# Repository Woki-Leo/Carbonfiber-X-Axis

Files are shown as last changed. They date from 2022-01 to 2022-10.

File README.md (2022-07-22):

# Lightweight X Axis Mod for the Voron 2.4 and Trident

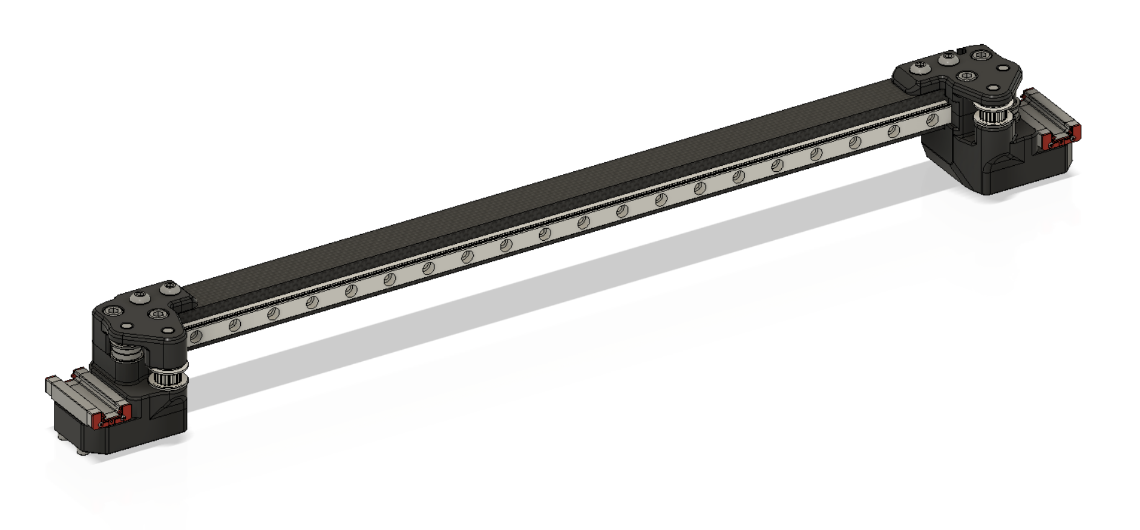
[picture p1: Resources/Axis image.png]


## What the goal is:

**Caution: the carbon tube will start soften at and above 60c chamber temperature!!**

- Removing lots of unnecessary weight to make the Printer go faster with better Quality
  - for a V2.4 350mm it drops the gantry weight from ~1350g to ~950g
    - 70g saved by removing the x drag chain
    - 150g saved by using the carbon tube
    - the rest is saved through the pinmod and other improvements
- Look good
- be usable for both MGN9 and MGN12

<br/>

## What's different:

- XY joints changes:
  - derived from the [pinmod](https://github.com/VoronDesign/VoronUsers/tree/master/printer_mods/hartk1213/Voron2.4_Pins_Mod)
  - room for MGN12 (heavily inspired by [arkeet](https://github.com/VoronDesign/VoronUsers/tree/master/printer_mods/arkeet/mgn12))
  - adjustment slots for the tube
  - removed unnecessary cutouts unter the y carriages (actually saves weight)
    - cut the corners at 45° here as well. Removes material that does nothing. 
- Chain delete --> umbilical receivers required

<br/>

## Required hardware:

- 20x20 1mm wall thickness carbon fiber tube 
  - you can use the original Alu tube as well but it will be very heavy
  - [you can find a fabricated tube here](https://www.aliexpress.com/item/1005004037790448.html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)
- 4PCs 5x40mm Pins (Use Carbon fiber rod)
- 4PCs M5x40 SHCS
- 10PCs M5 Nut
- 4PCs M5x12 BHCS
- 2PCs M5x30 BHCS

Using aluminium hardware for M5 is recommended. Watch out for the right alloy and heat treat! 7075 T6 is strongly recommended!

For rail mounting:
M3x8 SHCS + Nuts for the amount of screws you want (4-8 Recommended)

<br/>

## Required mods:

- MGN12: arkeet's [MGN12](https://github.com/VoronDesign/VoronUsers/tree/master/printer_mods/arkeet/mgn12) carriage or  jlas1' mgn12 [klicky](https://github.com/jlas1/Klicky-Probe/tree/main/Usermods/bluedragonx) carriage 
- MGN9: Ellis' [MGN9H](https://github.com/VoronDesign/VoronUsers/tree/master/printer_mods/Ellis/Single_MGN9H_Carriage) mod
- some sort of y endstop on the gantry (click [here](https://github.com/hartk1213/MISC/tree/main/Voron%20Mods/Voron%202/2.4/Voron2.4_Y_Endstop_Relocation) for hartk's AB endstop)
- until a clockwork umbilical holder is available the [gallileo](https://github.com/JaredC01/Galileo) clockwork is also needed

the rest is stock

<br/>

## Printing:

Please make sure you choose the right version for you printer!
Normally you should need the R2 Version with a new build. 
They are all printable without supports.
Settings: 
Standard voron settings.
or: drop perimeters and/or infill down to save weight 
3 perimeters and 20% infill tested

<br/>

## How to install it:

**Please be carefull with cf dust! Wear a respirator and safety glasses!**

1. Cut the carbon tube to your printers stock length (330mm for 250mm version for example)
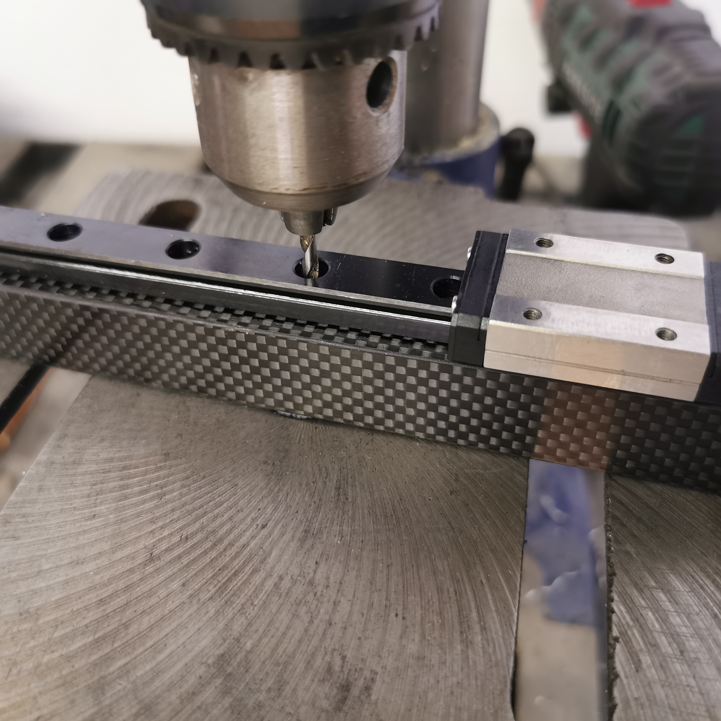
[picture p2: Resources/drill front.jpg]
2. (Drillpress recommended) Drill holes from the front through the tube centered using the rail as template. Use the choose the spacing to you liking. Center using the printed tool and measuring on either end. 3mm drill. Drill all the way through the tube. 
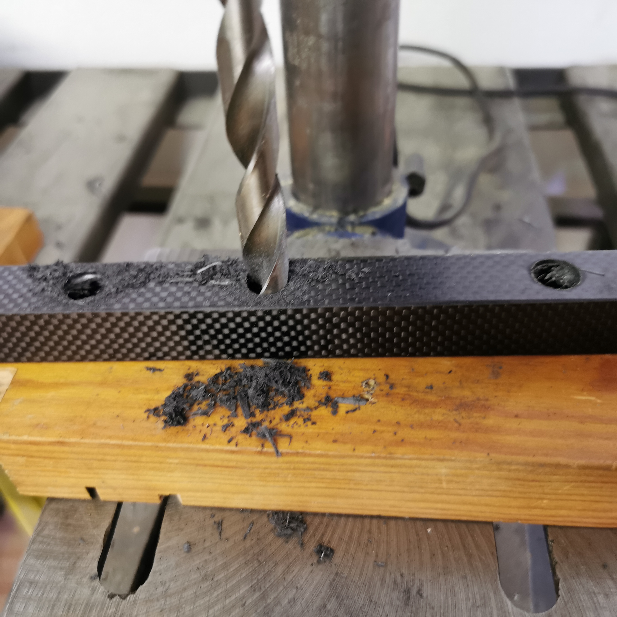
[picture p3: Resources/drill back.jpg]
3. Remove rail. Flip over and Drill from the back. Drill size has to be bigger than you M3 socket (12.5mm in my case). Take is slow to keep the blockout in the tube down.
4. Drill holes for the M5 Screws with 5.5mm drill
5. Debur
6. Assemble!

<br/>

## Things to come

- [x] MGN9 support
- [x] Adjustability between XY joints and carbon extrusion
- [x] Rework M5 nut holder inside the tube
- [ ] Umbilical holder for Clockwork and Galileo (Chain Delete)
- [ ] Alignment tool for drilling 5.5mm holes
- [ ] Drag chain mount on the carbon tube (for now you can glue it on)
- [ ] ~~20x20 1,5mm wall Carbon tube support~~ no benefit
- [ ] ~~Nut installing tool~~ not need since holes from the back make it so much simpler to install the M3 nuts for the rail

<br/>

##Contact

Feel free to reach out with any questions/suggestions you have!
Discord: Woki | Leo #8734

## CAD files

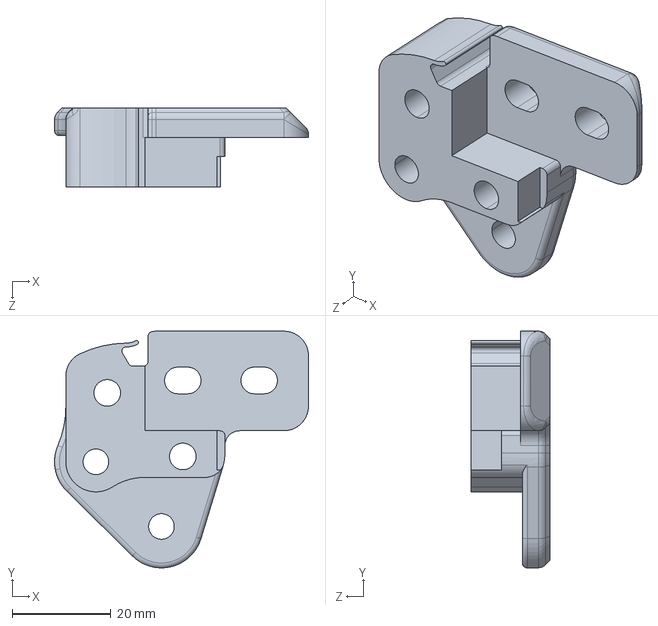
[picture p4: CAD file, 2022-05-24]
CAD/xy_joint_right_upper_MGN12 - CF.STEP
51.5 x 48.0 x 16.0 mm

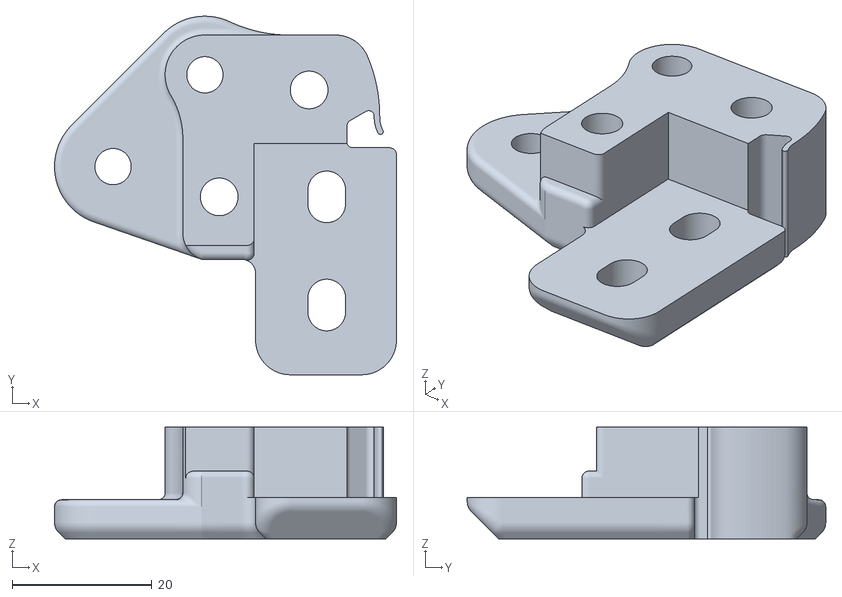
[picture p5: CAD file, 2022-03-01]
STLs/R1/R1_Right upper Carbon x1.stl
49.0 x 51.4 x 16.0

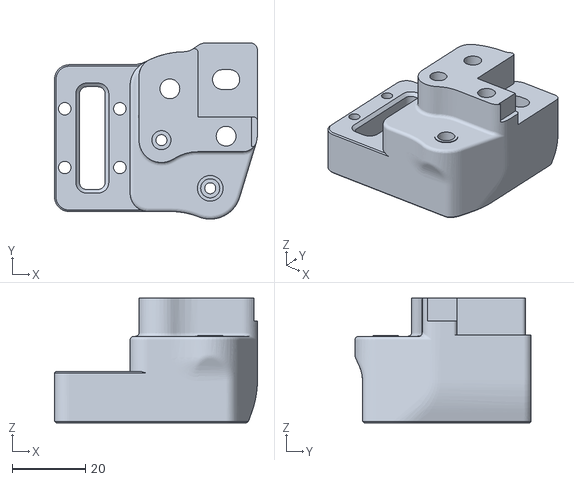
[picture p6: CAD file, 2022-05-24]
STLs/R2/R2_Left lower Carbon x1.STL
55.3 x 48.0 x 34.0

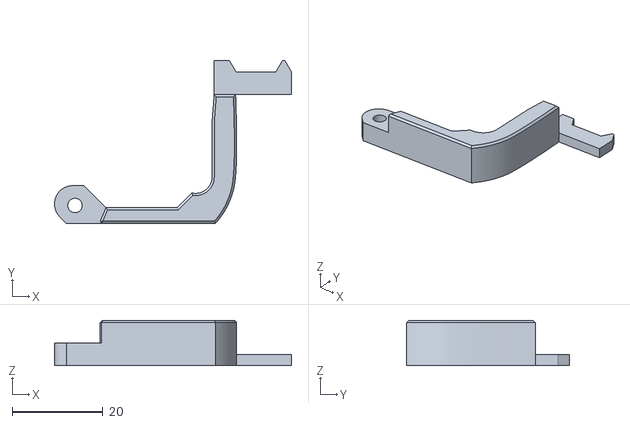
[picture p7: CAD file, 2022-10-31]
STLs/Umbilical Galileo Toolhead Receiver x1.stl
52.1 x 35.8 x 10.0

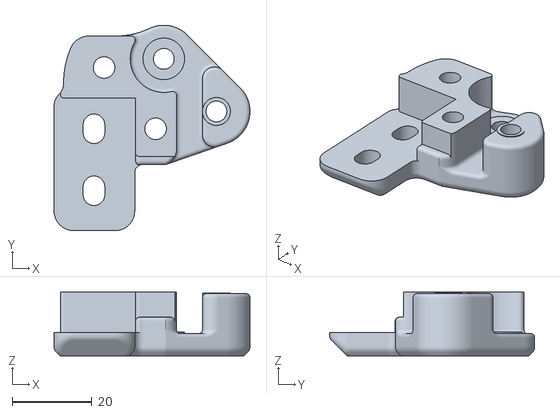
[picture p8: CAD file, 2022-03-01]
STLs/R1/R1_Left upper Carbon x1.stl
49.0 x 51.4 x 16.0

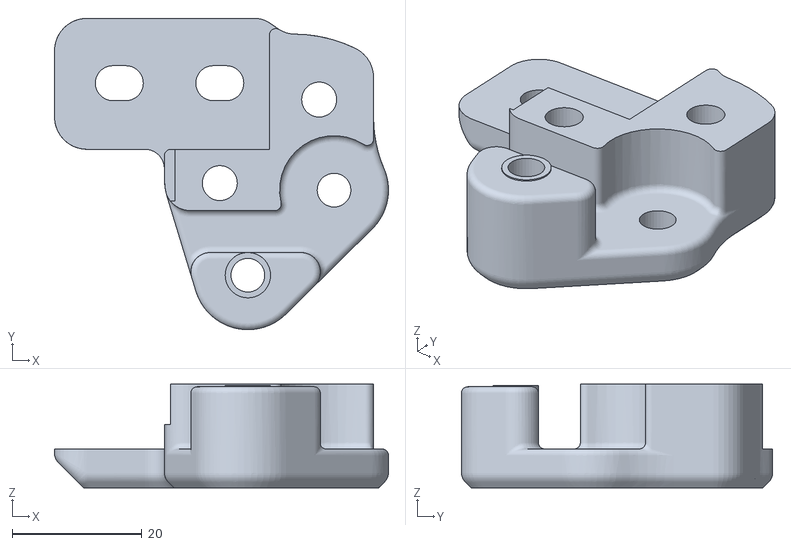
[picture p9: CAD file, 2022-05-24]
STLs/R2/R2_Left upper Carbon x1.STL
51.5 x 48.0 x 16.0

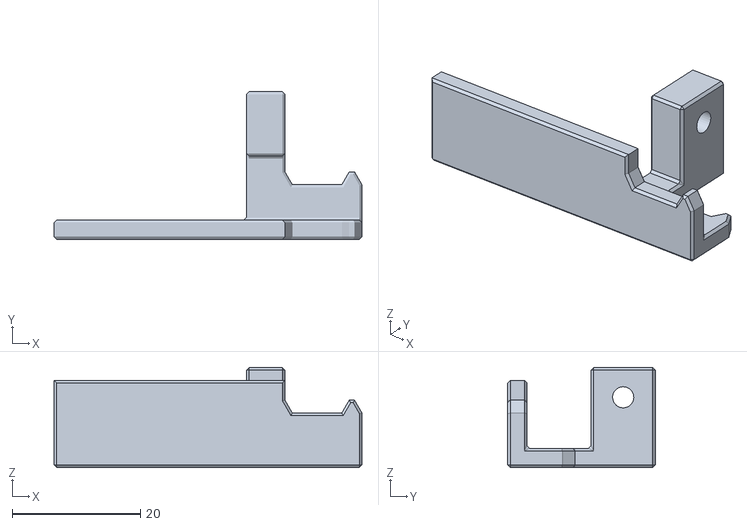
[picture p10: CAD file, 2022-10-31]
STLs/Umbilical Gantry Receiver x1.stl
48.0 x 23.0 x 15.6

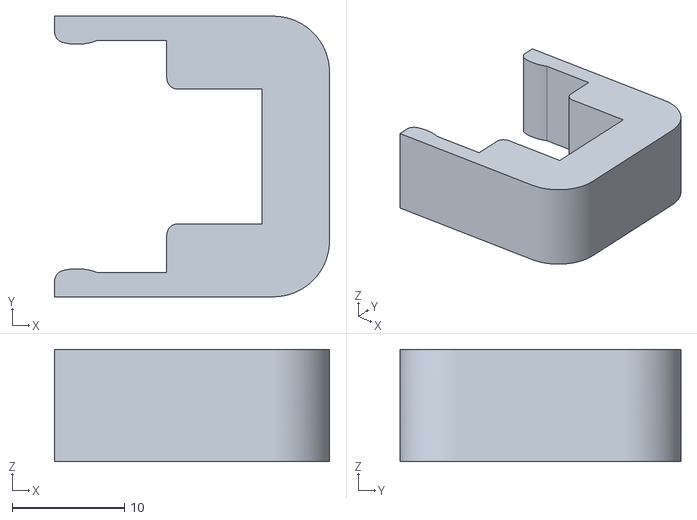
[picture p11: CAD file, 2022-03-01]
STLs/MGN12 Rail centering helper x2.stl
24.5 x 25.0 x 10.00

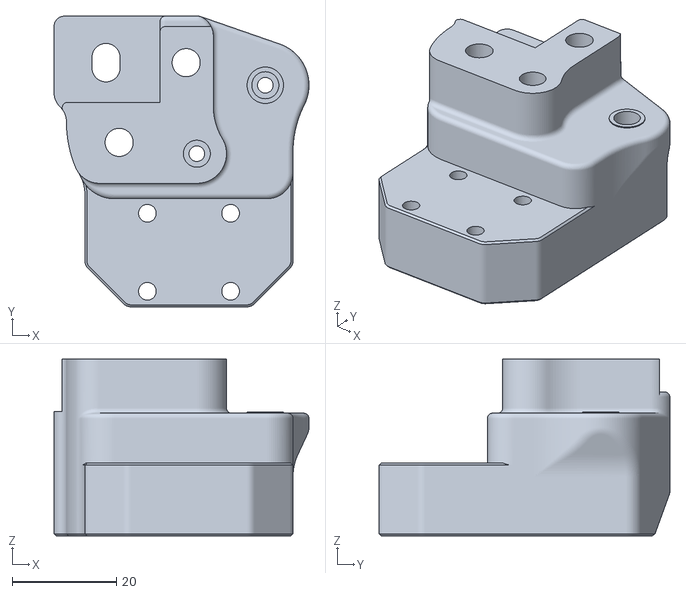
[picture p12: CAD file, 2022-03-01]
STLs/R1/R1_Left lower Carbon x1.stl
49.0 x 55.9 x 34.0

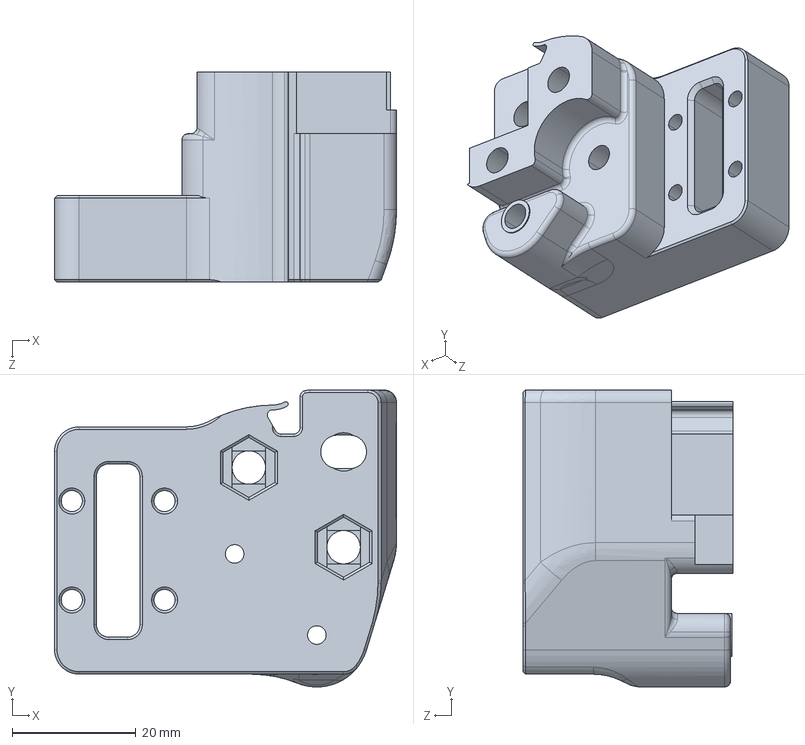
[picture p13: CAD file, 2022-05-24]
CAD/xy_joint_right_lower_MGN12 - CF.STEP
55.3 x 48.0 x 34.0 mm

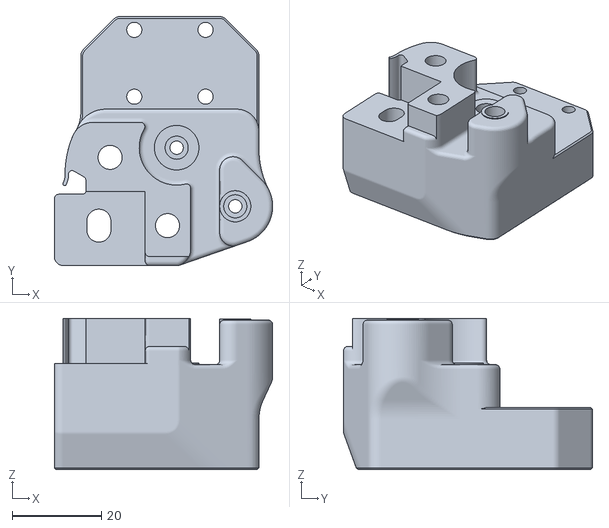
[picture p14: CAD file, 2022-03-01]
STLs/R1/R1_Right lower Carbon x1.stl
49.0 x 55.9 x 34.0

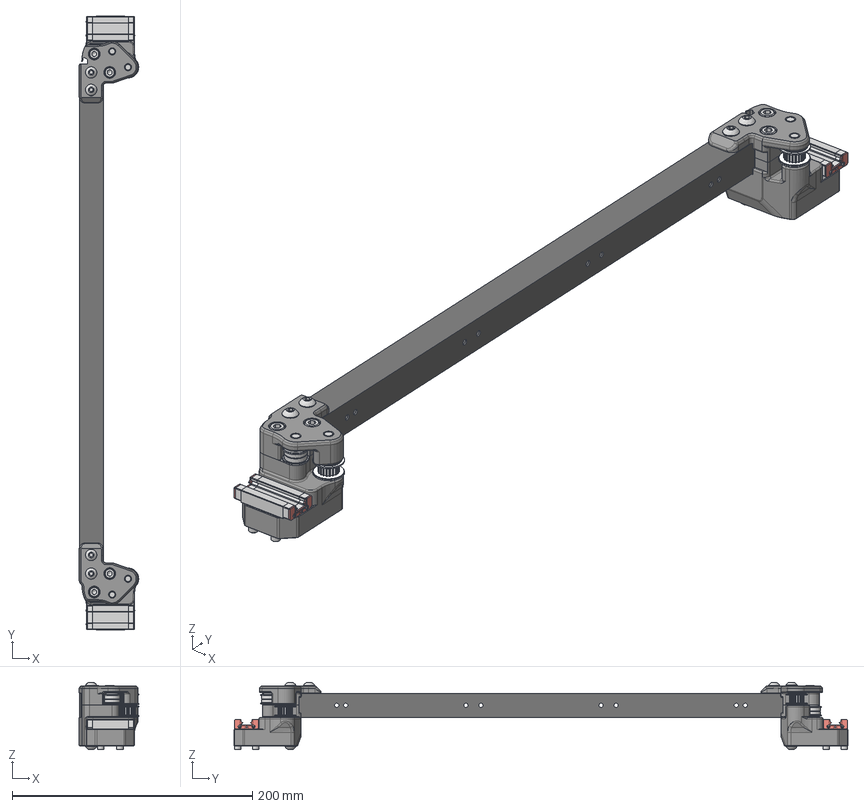
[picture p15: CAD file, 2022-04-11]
CAD/Carbon fiber mod.step
49.6 x 511.0 x 56.0 mm
GT2 20T Idler Gates v2
GT2 20T Idler v3 (2)
M5 Hex Nut x 2
M5x30 BHCS (1)
M3x20 SHCS (2) x 4
M5x40 SHCS (2) x 2
M5 1mm Spacer (1) x 2
F695 ZZ (1) x 2
MGN9H - Carriage (9)
MGN9H - Carriage (1) (1)
MGN9H - Carriage (2) (1)
MGN9H - Carriage (3) (1)
MGN9H - Carriage (4) (1)
MGN9H - Carriage (5) (1)
MGN9H - Carriage (6) (1)
MGN9H - Carriage (7) (1)
MGN9H - Carriage (8) (1)
5x40 Pin
5x40 Pin (1)
M5x10 BHCS x 2
MGN9H - Carriage (9)_1
MGN9H - Carriage (1) (1)_1
MGN9H - Carriage (2) (1)_1
MGN9H - Carriage (3) (1)_1
MGN9H - Carriage (4) (1)_1
MGN9H - Carriage (5) (1)_1
MGN9H - Carriage (6) (1)_1
MGN9H - Carriage (7) (1)_1
MGN9H - Carriage (8) (1)_1
GT2 20T Idler Gates v2_1
M3x20 SHCS (2)_1 x 4
M5x40 SHCS (2)_1 x 2
M5x30 BHCS (1)_1
M5 1mm Spacer (1)_1 x 2
F695 ZZ (1)_1 x 2
GT2 20T Idler v3 (2)_1
M5 Hex Nut_1 x 2
5x40 Pin_1
5x40 Pin (1)_1
M5x10 BHCS_1 x 2
Inserts
Carbon tube 350mm^2

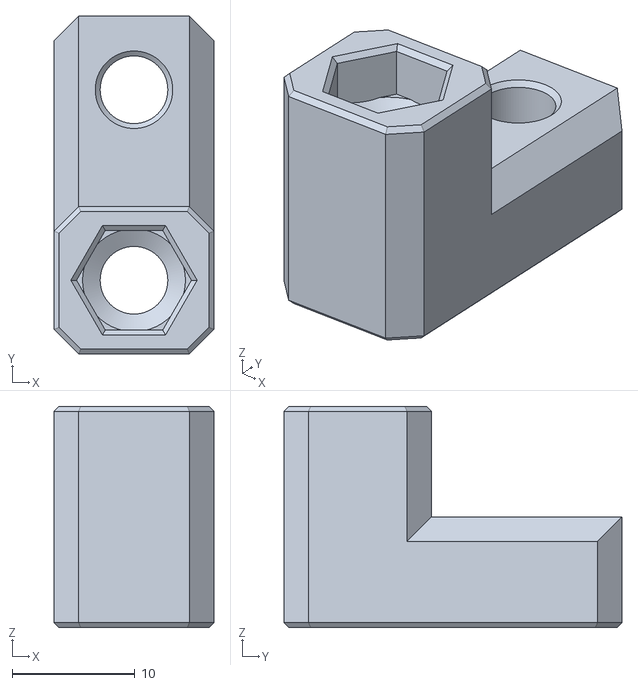
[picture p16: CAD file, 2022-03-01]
STLs/Nut Holder x2.stl
13.0 x 27.5 x 18.0

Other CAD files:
CAD/xy_joint_left_lower_MGN12 - CF.STEP
CAD/xy_joint_left_upper_MGN12 - CF.STEP
STLs/R2/R2_right upper Carbon x1.STL
STLs/MGN9 Rail centering helper x2.stl
STLs/R2/R2_right lower Carbon x1.STL

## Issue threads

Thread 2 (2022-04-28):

need to update for 2.4r2

dmitryuv, 2022-04-28:
Hi,

XY joints needs to be updated for 2.4r2, so most of the parts can be used form the original STLs (like carriage) and not from (outdated) MODs.

Specifically:
- shafts are now a bit closer to the rail, since new belts design press fit them agains the rail carriage, shifting their original position closer. With your current design belts won't be parallel to the rail.
- I'm not sure it makes sense to have cut corners without middle cut (as in the original design). You took off some material at the corners, but added in the middle. By slicer estimations there are no savings at all (not even 1g). I propose revert to the original here.

I've added comparison of the both parts (original and modified) and highlighted the difference in the shaft positions.

Thanks
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
!

Woki-Leo, 2022-04-28:
Hey,

i currently have no time to do the changes needed for v2.4r2.

The material in the center slot was added because the walls for the slot added more material than they saved (this was tested with 20% + 2 walls) and it takes away strength and stiffness. not shure why it was there in the first place.
The camfers were my personal stylistic choice.

Feel free to modify it to your liking and open a Pull request!

dmitryuv, 2022-04-28:
I'm currently in the process of modifying r2 joints, but i'm working from original CAD files to since changing STL mesh won't have the same end-quality. Unfortunately I won't be able to re-create your changes, so if you're OK I can later make pull request that will only include holes adjustments and rods mod.

dmitryuv, 2022-04-28:
yes, the CAD version of the non-r2 joint :) it's much harder to move around core dimensions than expand few holes, that's why i took original to modify.

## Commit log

2022-01-06 prerelease version 0.1
    [Gallileo umbilical receiver.stl, Gantry umbilical receiver.stl, Left lower Carbon.stl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]
2022-01-06 added printed parts image
2022-01-17 prerelease version 0.2
    [Gallileo umbilical receiver x1.stl, Gantry umbilical receiver x1.stl, Left lower Carbon x1.stl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]
2022-03-01 Updated STLs and added Aliexpress link
    [Left lower Carbon x1.stl, Left upper Carbon x1.stl, Right lower Carbon x1.stl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]
2022-03-01 oriented STLs
    [Gallileo umbilical receiver x1.stl, Gantry umbilical receiver x1.stl, Left upper Carbon x1.stl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]
2022-04-07 Added heat warning
2022-04-11 Add CAD data
    [Carbon fiber mod.step]
2022-05-17 Added r2 compatible XY Joints
    [Left lower Carbon x1.stl, Left upper Carbon x1.stl, Right lower Carbon x1.stl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]
2022-05-24 Clean folder structure and naming
    [R1_Left lower Carbon x1.stl, R1_Left upper Carbon x1.stl, R1_Right lower Carbon x1.stl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]
2022-07-17 Update README.md
    BOM correction
2022-10-31 Stronger umbilical strain-relief parts
    [Gallileo umbilical receiver x1.stl, Gantry umbilical receiver x1.stl, Umbilical Galileo Toolhead Receiver x1.stl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]
